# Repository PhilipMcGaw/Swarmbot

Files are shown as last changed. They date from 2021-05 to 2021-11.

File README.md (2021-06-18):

# SwarmBot

## Physical design constraints

* Smallest 3D Printer maximum dimensions 100 x 100 x 100
* Largest Cheap PCB from China 100 x 100 FR4 (50¢ each)

## People who have contributed

 * Philip 'Skippy' McGaw - philip@mcgaw.eu - [philipmcgaw.com](https://philipmcgaw.com)
 * Tamarisk 'NotQuiteHere' McGaw - tamarisk@mcgaw.eu - [tamarisk.it](https://tamarisk.it)
 * Bob 'thinkl33t' Clough - bob@clough.me - [thinkl33t.co.uk](https://thinkl33t.co.uk)

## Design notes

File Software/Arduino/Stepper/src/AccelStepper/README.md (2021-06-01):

This fork follows the [upstream version](http://www.airspayce.com/mikem/arduino/AccelStepper/). Files are slightly reorganised to follow Arduino library conventions to allow for inclusion into the Arduino IDE library manager.

Please direct questions and discussion to [the Google group](http://groups.google.com/group/accelstepper)

---

This is the Arduino AccelStepper library. It provides an object-oriented interface for 2, 3 or 4 pin stepper motors and motor drivers.

The standard Arduino IDE includes the [Stepper library](http://arduino.cc/en/Reference/Stepper) for stepper motors. It is perfectly adequate for simple, single motor applications.

AccelStepper significantly improves on the standard Arduino Stepper library in several ways:

  - Supports acceleration and deceleration
  - Supports multiple simultaneous steppers, with independent concurrent stepping on each stepper
  - API functions never delay() or block
  - Supports 2, 3 and 4 wire steppers, plus 3 and 4 wire half steppers.
  - Supports alternate stepping functions to enable support of [AFMotor](https://github.com/adafruit/Adafruit-Motor-Shield-library)
  - Supports stepper drivers such as the Sparkfun EasyDriver (based on 3967 driver chip)
  - Very slow speeds are supported
  - Extensive API
  - Subclass support

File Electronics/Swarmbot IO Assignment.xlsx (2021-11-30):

Pin # | Function | GPIO Number | ADC Number | PWM | KiCad
1 | GND |  |  |  | GND
2 | 3V3 |  |  |  | 3V3
3 | Enable |  |  |  | enable
4 | Sensor_VP | 36 | 0 | yes | IR 1 | Analouge in
5 | Sensor_VN | 39 | 3 | yes | IR 2 | Analouge in
6 | IO34 | 34 | 6 | yes | IR 3 | Analouge in
7 | IO35 | 35 | 7 | yes | IR 4 | Analouge in
8 | IO32 | 32 | 4 | yes | IR 5 | Analouge in
9 | IO33 | 33 | 5 | yes | Bat V | Analouge in
10 | IO25 | 25 | 18 | yes | Bat I | Analouge in
11 | IO26 | 26 | 19 | yes | Top PCB Version | Analouge in
12 | IO27 | 27 | 17 | yes | Bottom PCB Version | Analouge in
13 | IO14 | 14 | 16 | yes | Line Sensor 5 | Analouge in
14 | IO12 | 12 | 15 | yes | Line Sensor 3 | Analouge in
15 | GND |  |  |  | GND
16 | IO13 | 13 | 14 | yes | Line Sensor 1 | Analouge in
17 | SD2 | 9 |  | yes | Motor PWM 1 | Digital out (PWM)
18 | SD3 | 10 |  | yes | Motor PWM 2 | Digital out (PWM)
19 | CMD | 11 |  | yes | Motor PWM 3 | Digital out (PWM)
20 | CLK | 6 |  | yes | Motor PWM 4 | Digital out (PWM)
21 | SDO | 7 |  | yes | Left Switch | Digital in
22 | SD1 | 8 |  | yes | Line Sensor LED | Digital out
23 | IO15 | 15 | 13 | yes | Line Sensor 4 | Analouge in
24 | IO2 | 2 | 12 | yes | Line Sensor 2 | Analouge in
25 | IO0 | 0 | 11 | yes | program
26 | IO4 | 4 | 10 | yes | IR LEDS | Digital out
27 | IO16 | 16 |  | yes | Pen Servo | Digital in
28 | IO17 | 17 |  | yes | Right Motor Sensor | Digital in
29 | IO5 | 5 |  | yes | 5V Switch 1 | Digital out
30 | IO18 | 18 |  | yes | Left Motor Sensor | Digital in
31 | IO19 | 19 |  | yes | Sonar Echo | Digital in
32 | n/c |  |  |  | n/c
33 | IO21 | 21 |  | yes | Sonar Trigger | Digital out
34 | RXD0 | 3 |  | yes | RX
35 | TXD0 | 1 |  | yes | TX
36 | IO22 | 22 |  | yes | Right Switch | Digital in
37 | IO23 | 23 |  | yes
38 | GND |  |  |  | GND

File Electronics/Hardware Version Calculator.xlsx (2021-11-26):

Input voltage | 3.3 | Hardware revision ID | R1 Value | R2 Value | Vout | Mapped value
Top Value for map | 100 | 1 | 10 | 0 | 0 | 0
 |  | 2 | 47 | 1 | 0.06875 | 2
 |  | 3 | 10 | 1 | 0.3 | 9
 |  | 4 | 4.7 | 1 | 0.5789473684 | 18
 |  | 5 | 2.2 | 1 | 1.03125 | 31
 |  | 6 | 4.7 | 2.2 | 1.052173913 | 32
 |  | 7 | 10 | 10 | 1.65 | 50
 |  | 8 | 4.7 | 10 | 2.244897959 | 68
 |  | 9 | 1 | 2.2 | 2.26875 | 69
 |  | 10 | 2.2 | 10 | 2.704918033 | 82
 |  | 11 | 4.7 | 47 | 3 | 91
 |  | 12 | 2.2 | 47 | 3.152439024 | 96
 |  | 13 | 1 | 47 | 3.23125 | 98
 |  | 14 | 0 | 10 | 3.3 | 100

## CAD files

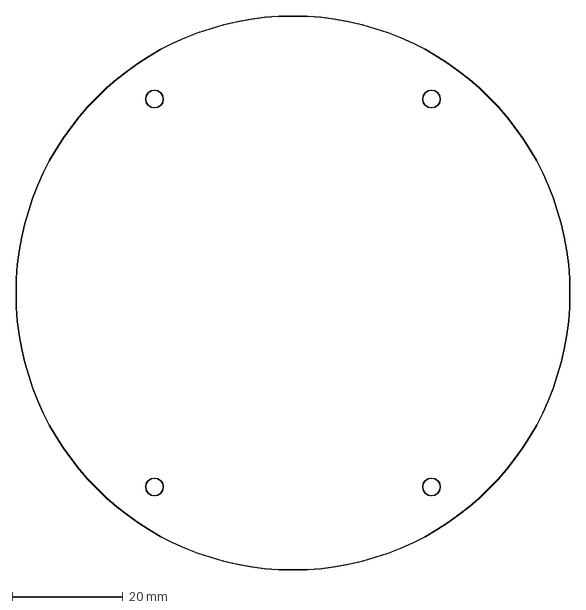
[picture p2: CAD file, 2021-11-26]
Electronics/Swarmbot Top PCB - Edge Cuts.dxf
100.0 x 100.0 mm

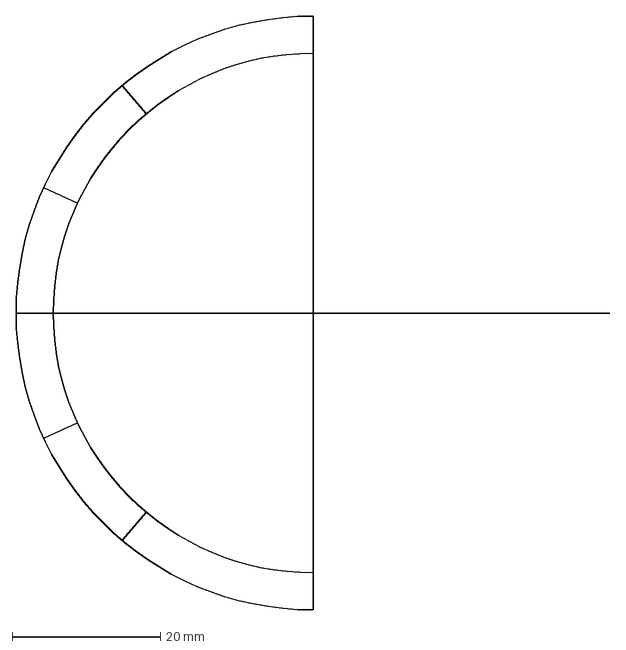
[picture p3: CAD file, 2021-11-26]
Electronics/Swarmbot Top PCB - User.2.dxf
80.0 x 80.0 mm

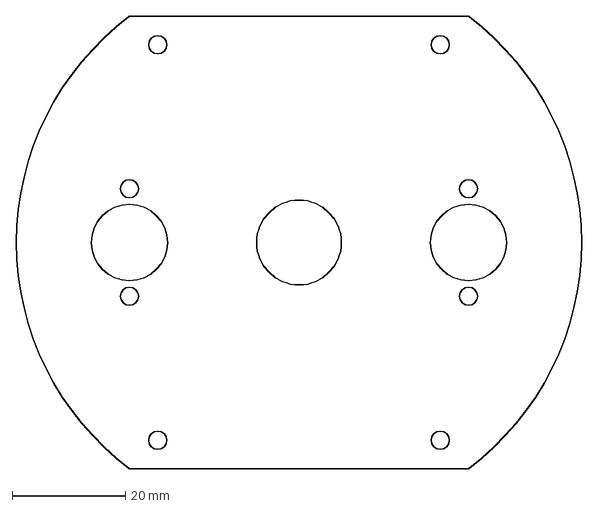
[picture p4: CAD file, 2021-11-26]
Electronics/Swarmbot Bottom PCB - Edge Cuts.dxf
100.0 x 80.0 mm

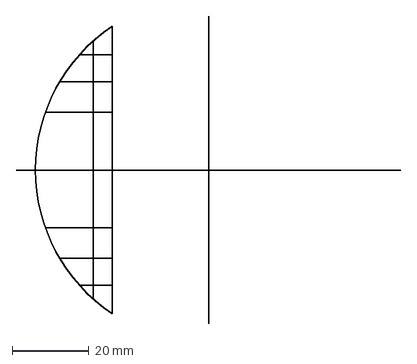
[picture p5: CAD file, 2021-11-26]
Electronics/Swarmbot Bottom PCB - User.2.dxf
100.0 x 80.0 mm

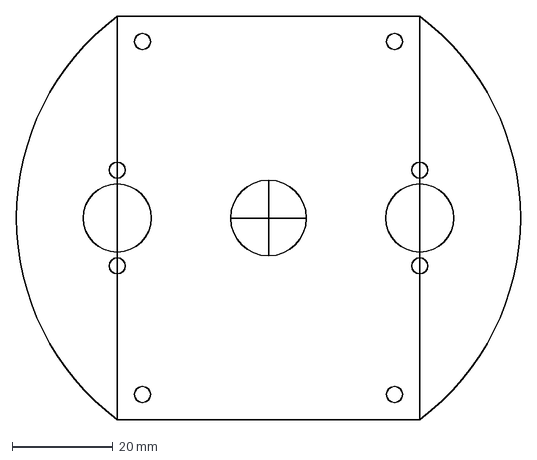
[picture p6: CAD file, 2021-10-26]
Electronics/Swarmbot v2.dxf
100.0 x 80.0 mm

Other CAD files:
Mechanical/Swarmbot Assembly.f3d

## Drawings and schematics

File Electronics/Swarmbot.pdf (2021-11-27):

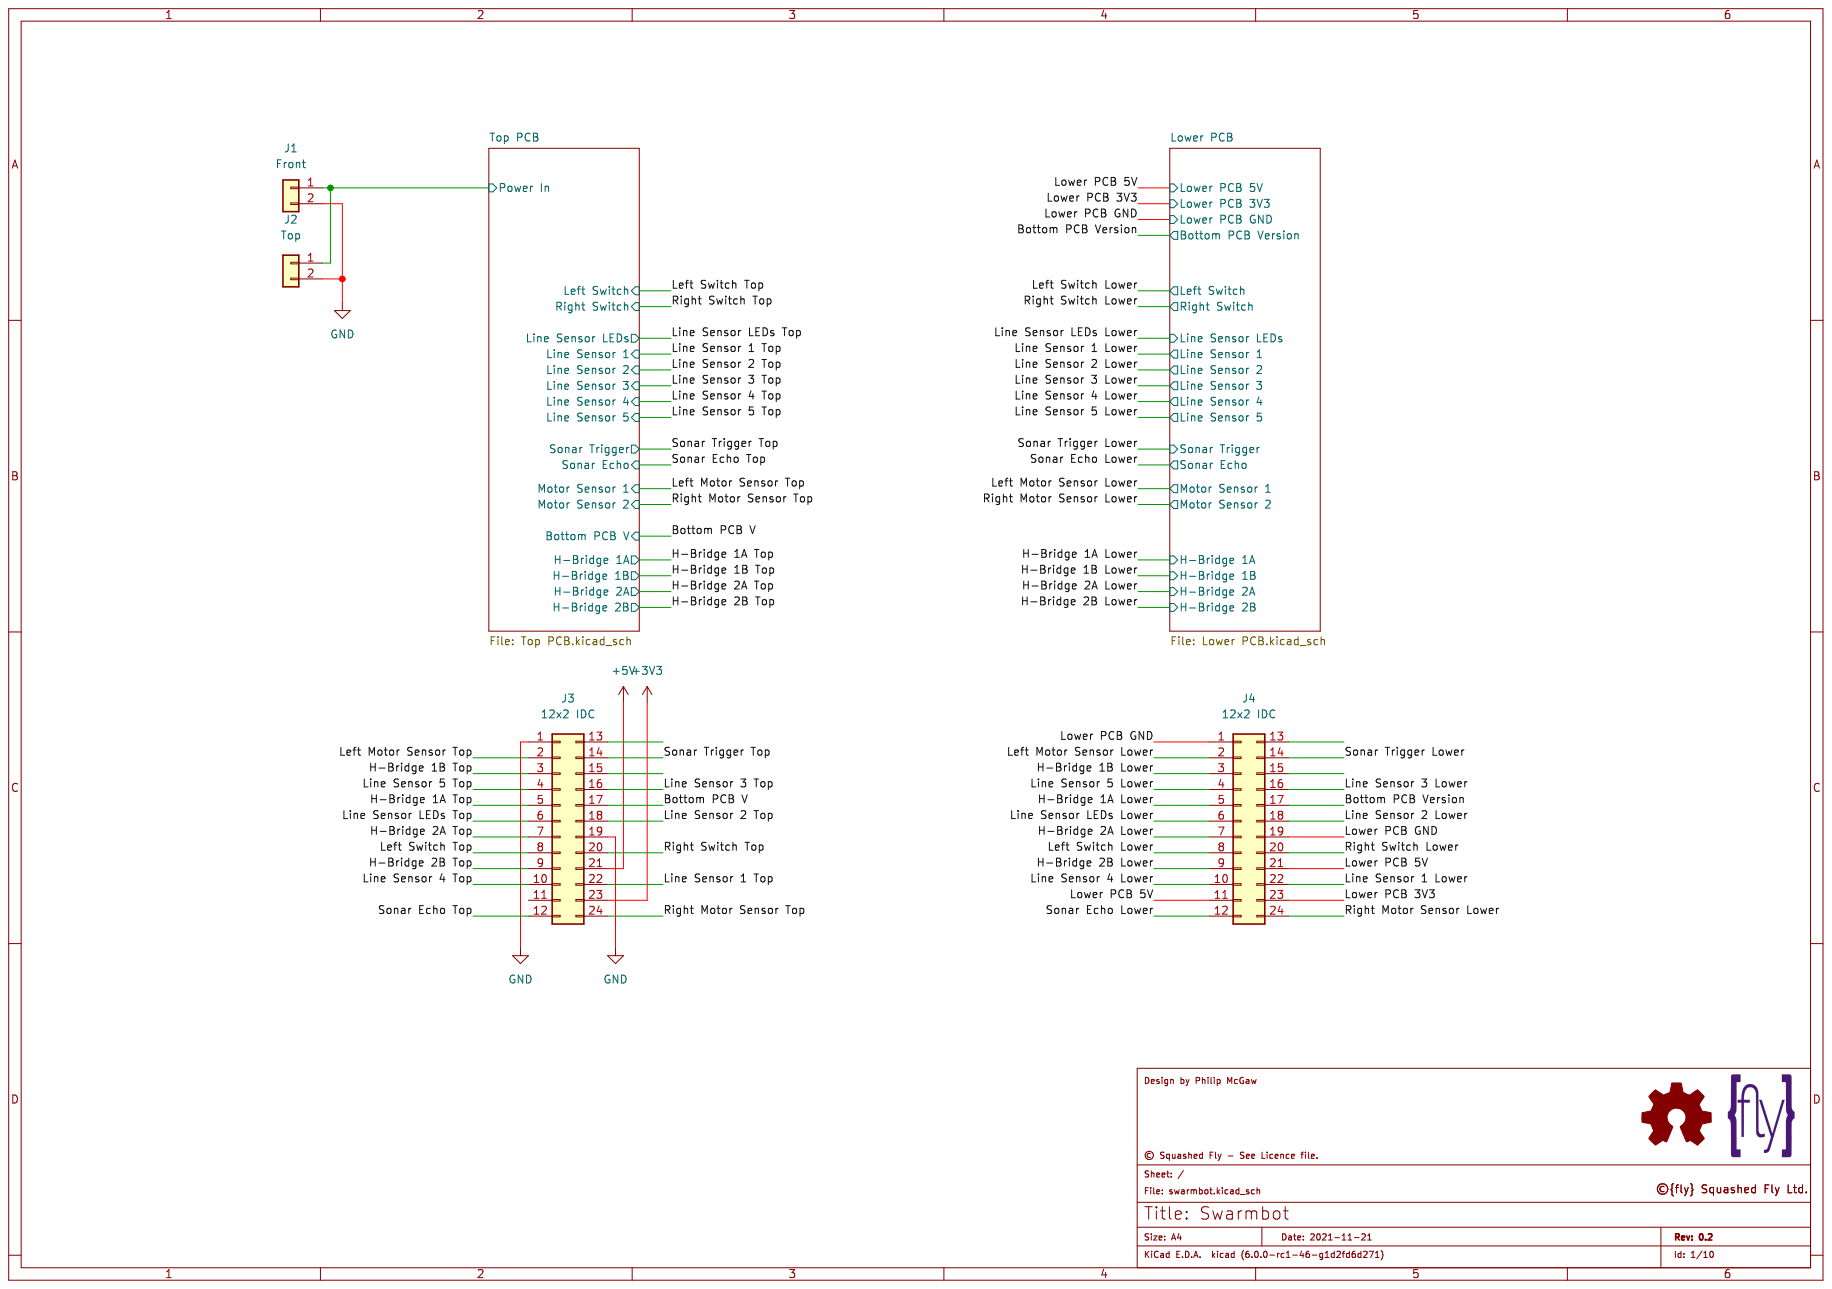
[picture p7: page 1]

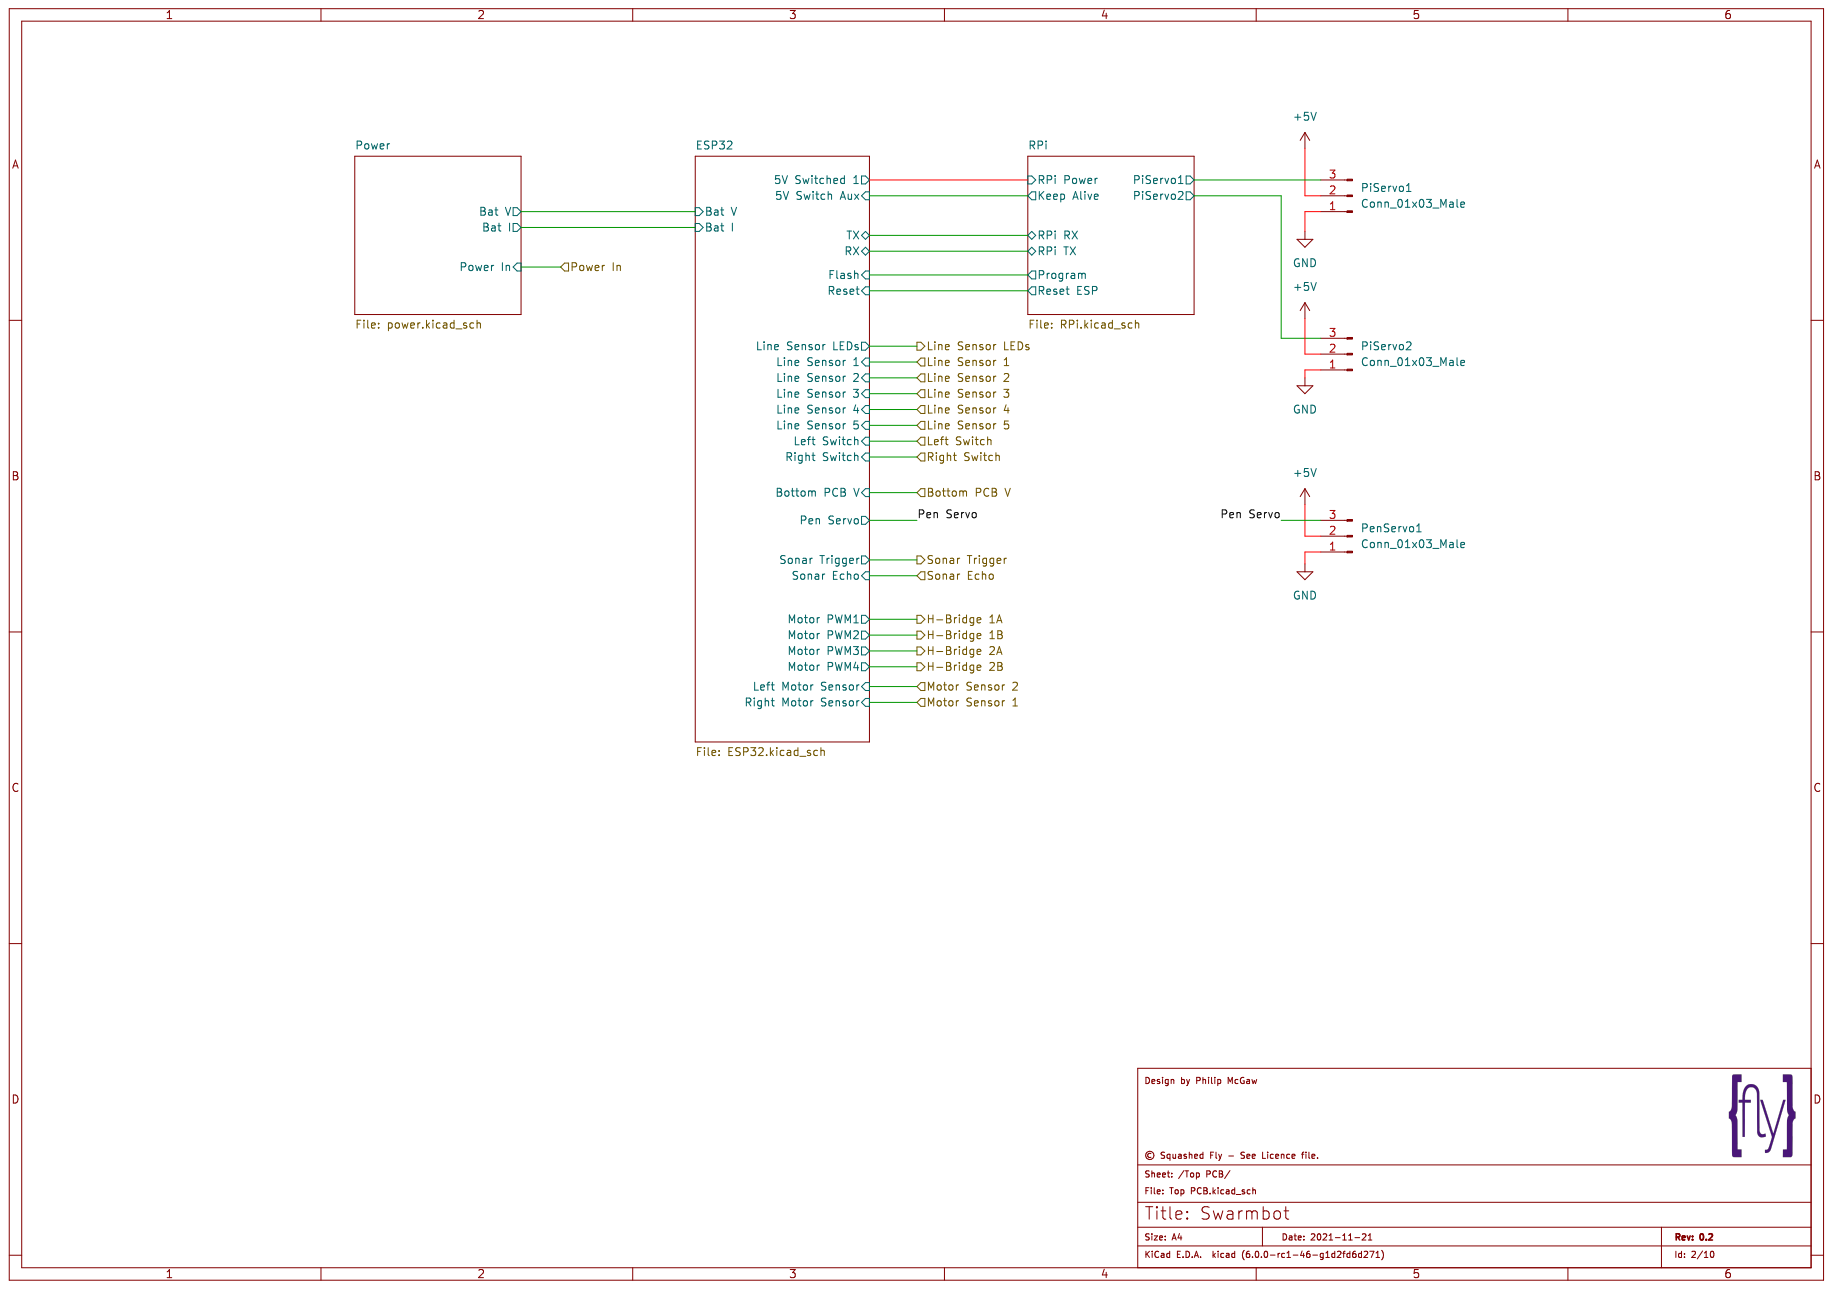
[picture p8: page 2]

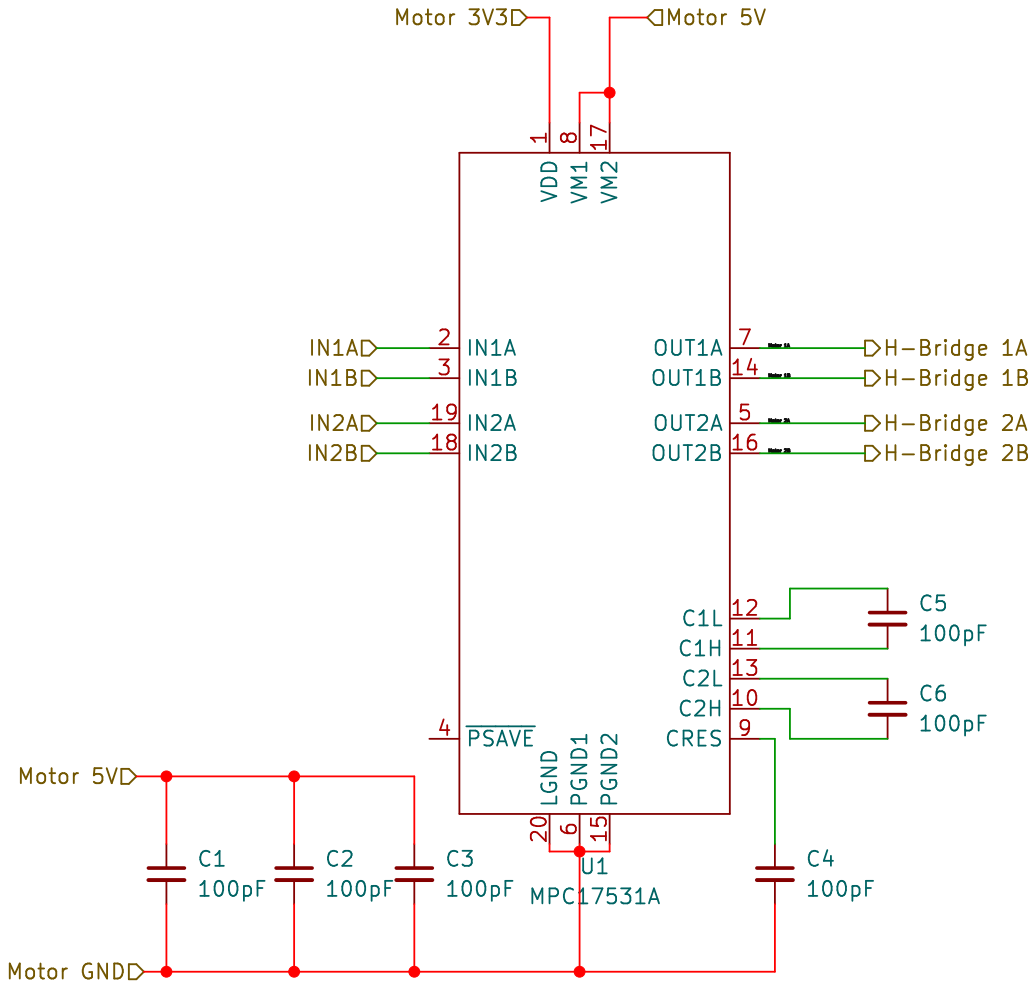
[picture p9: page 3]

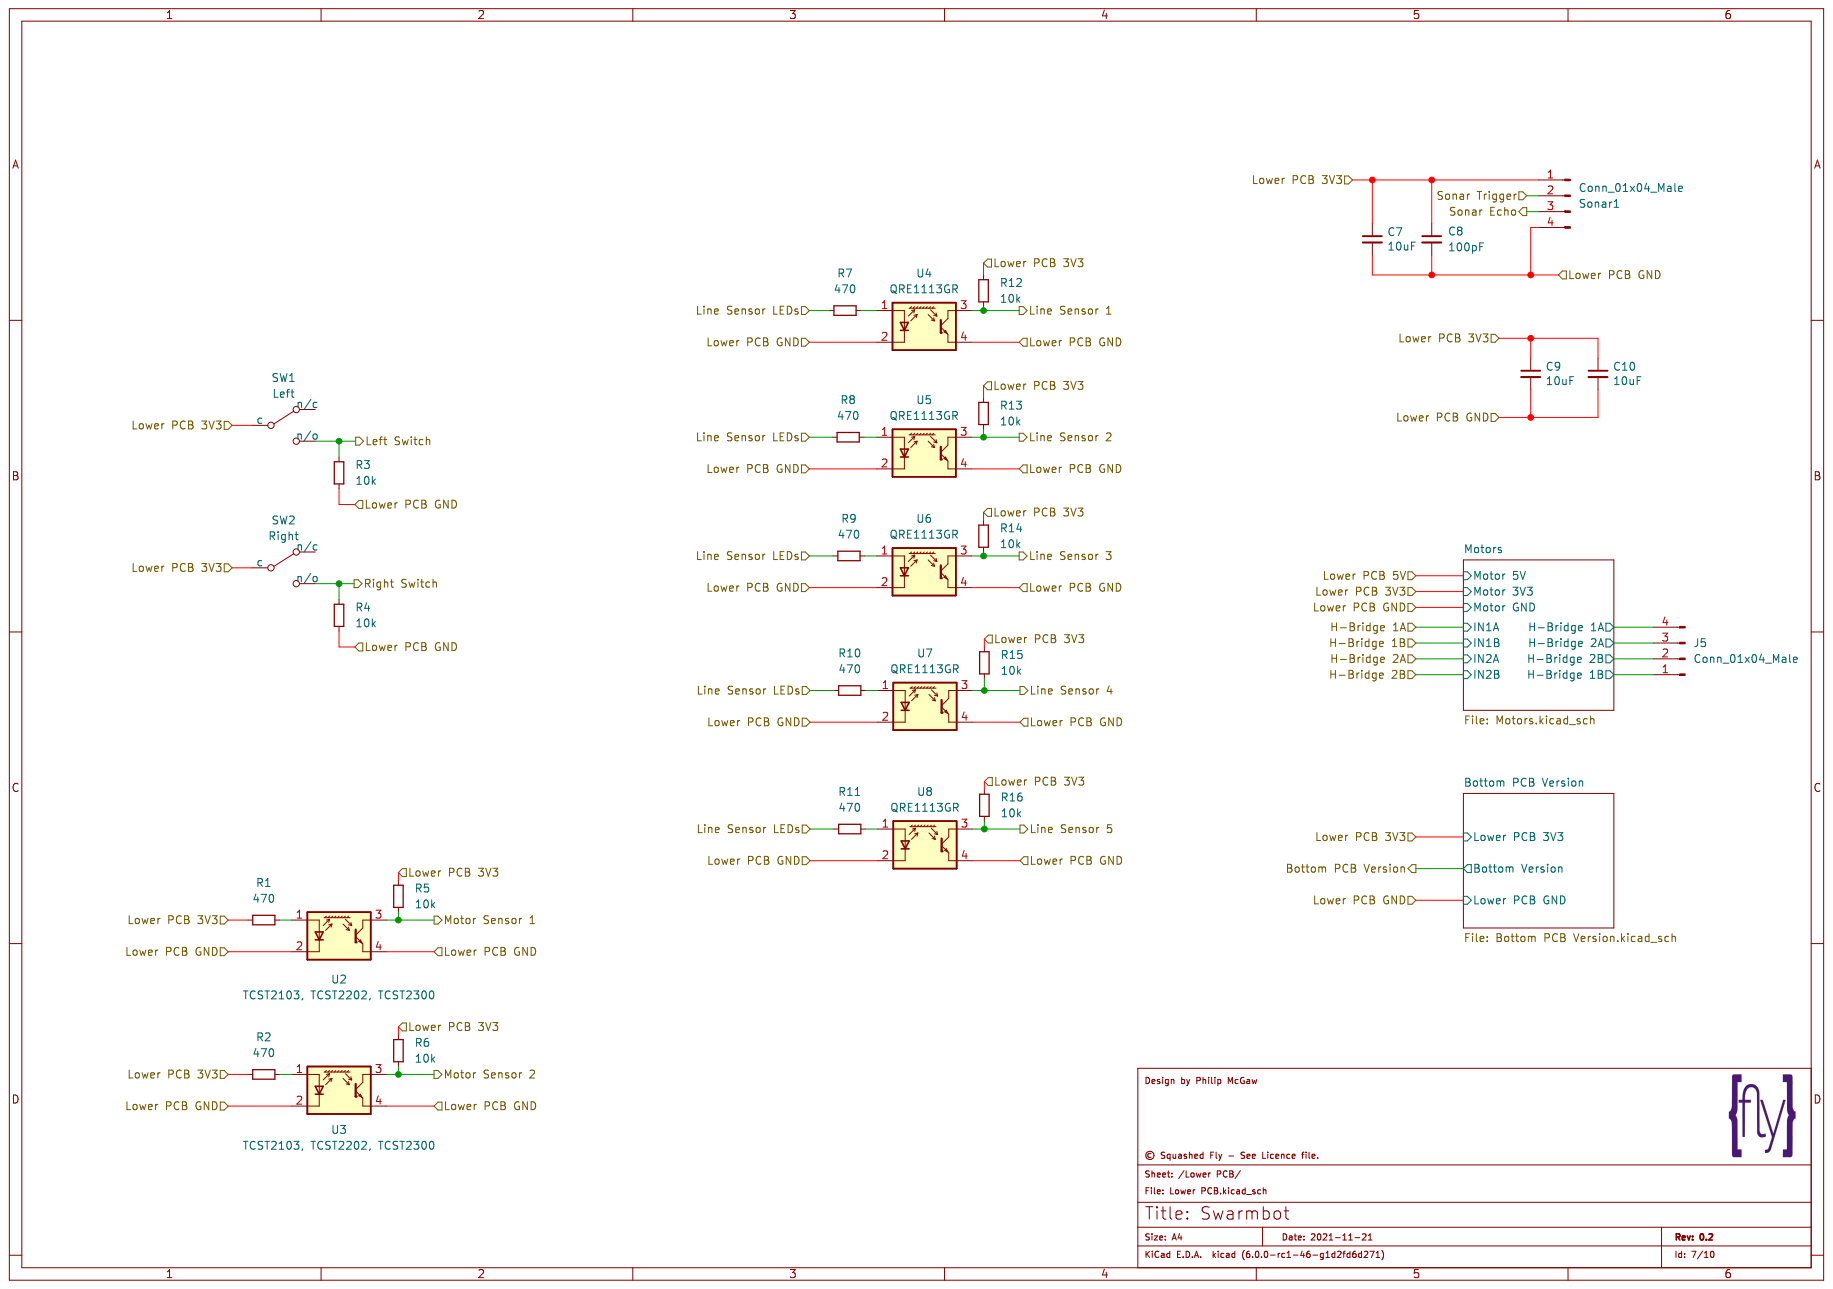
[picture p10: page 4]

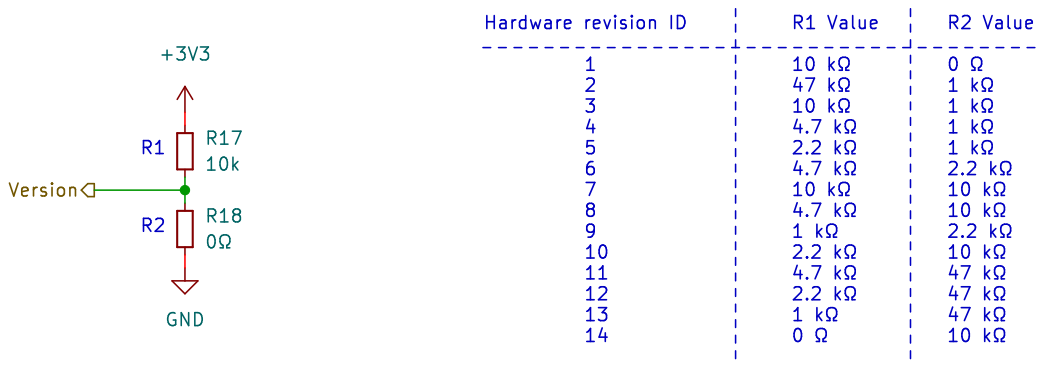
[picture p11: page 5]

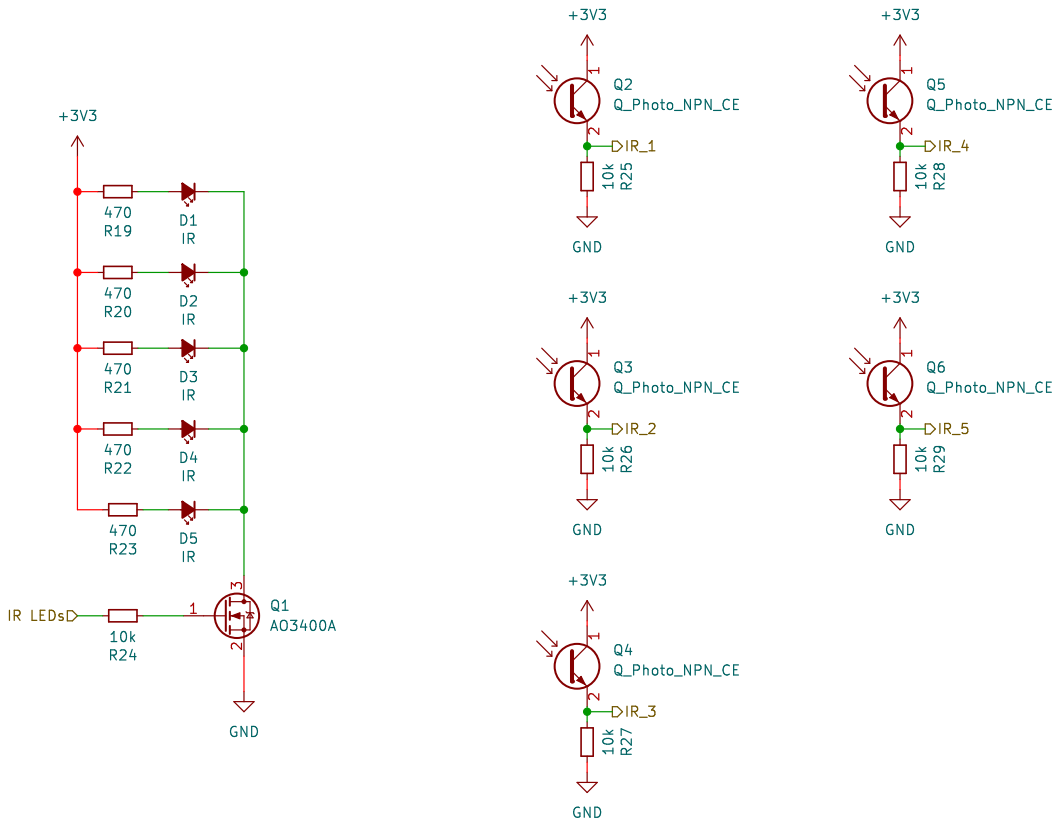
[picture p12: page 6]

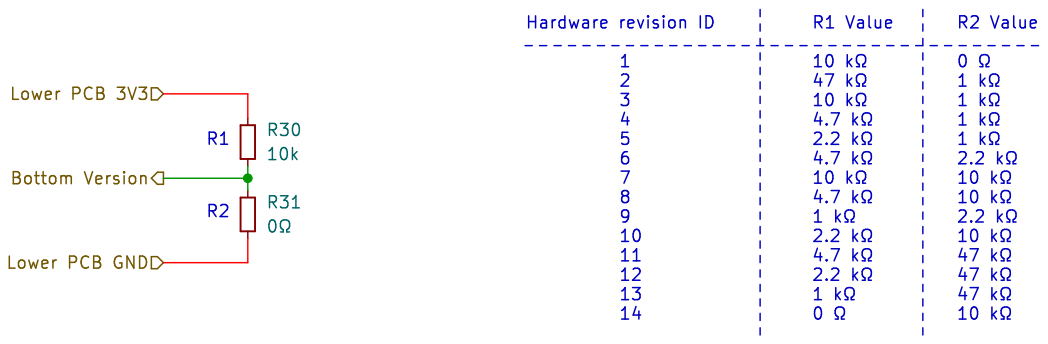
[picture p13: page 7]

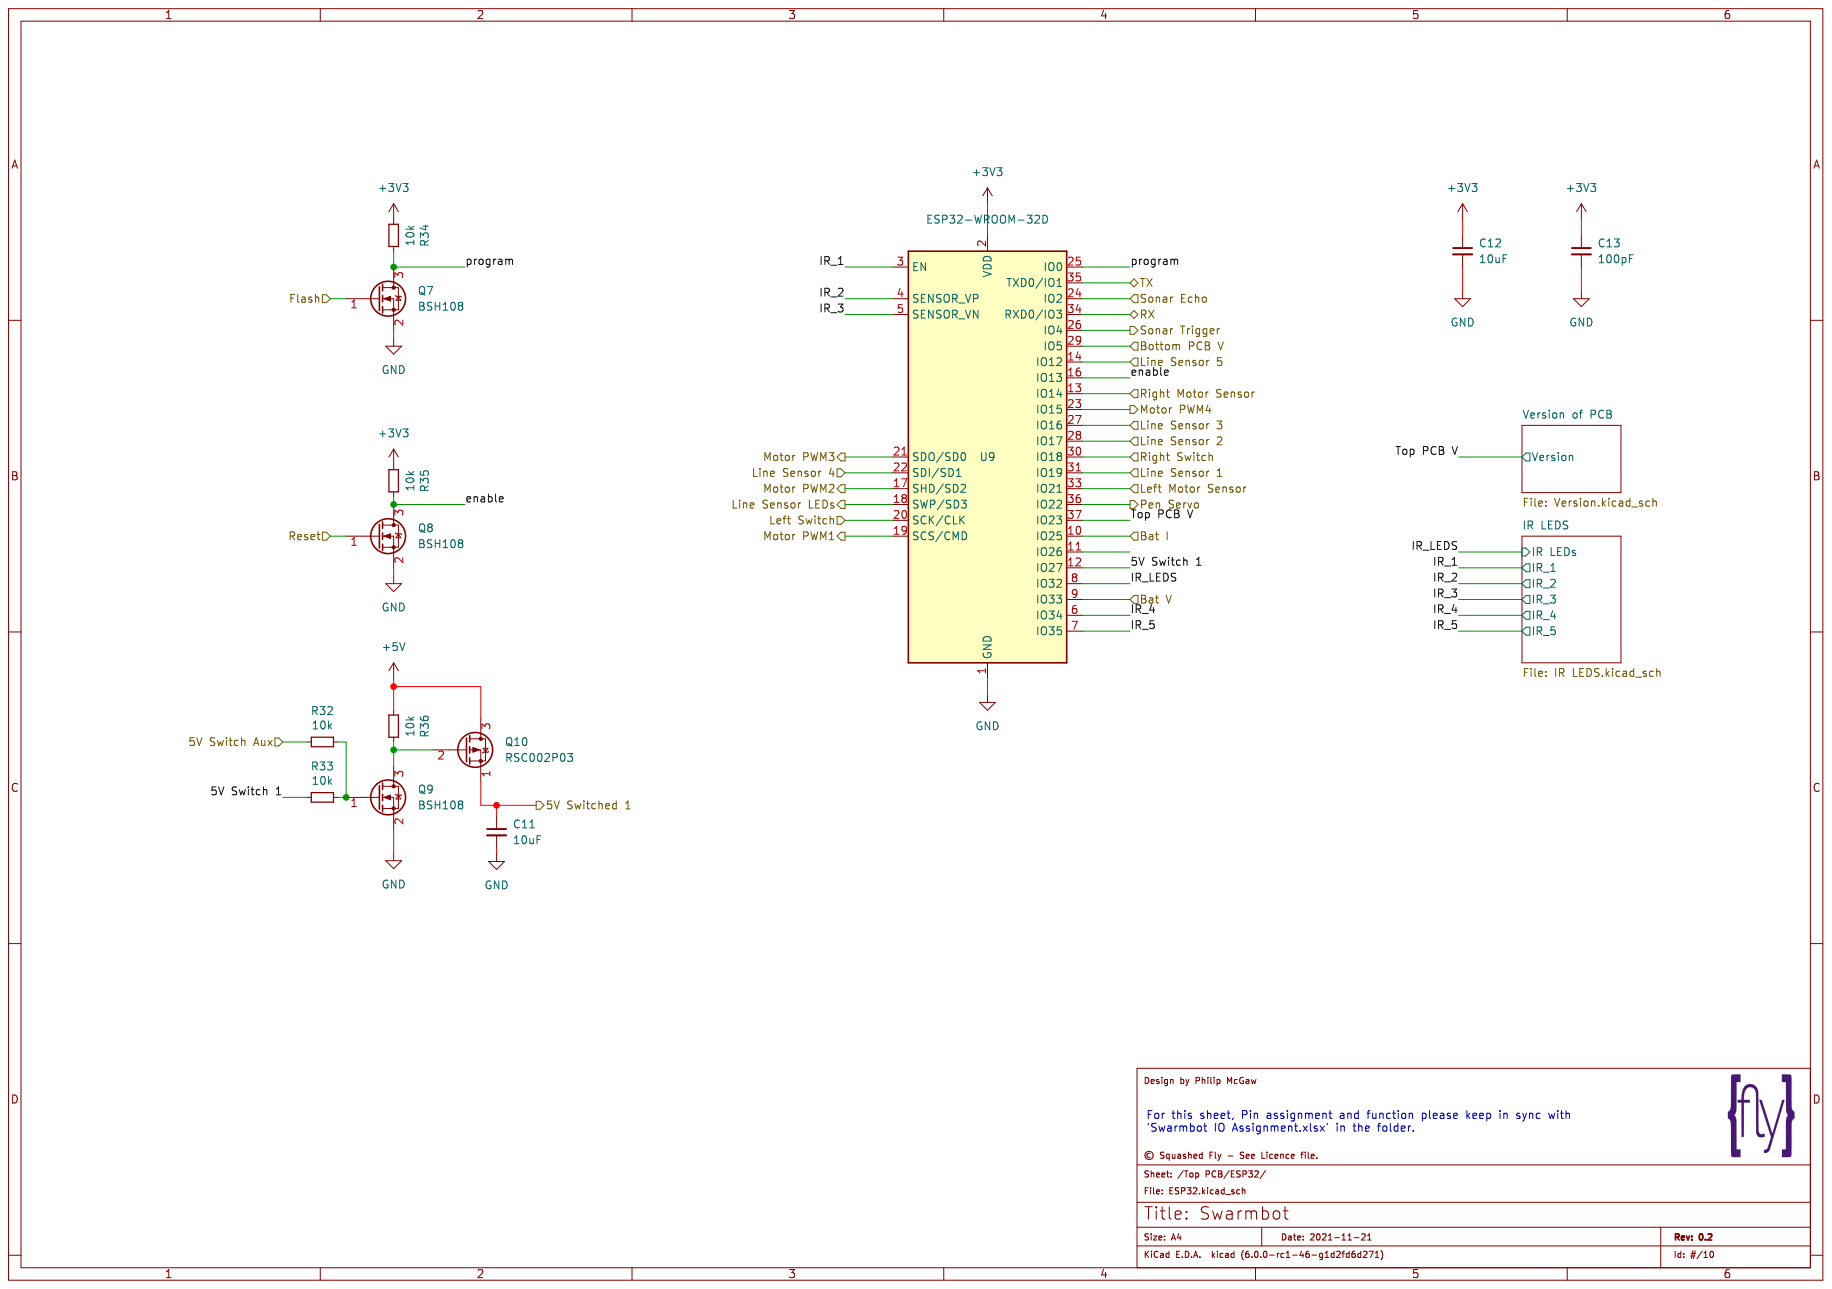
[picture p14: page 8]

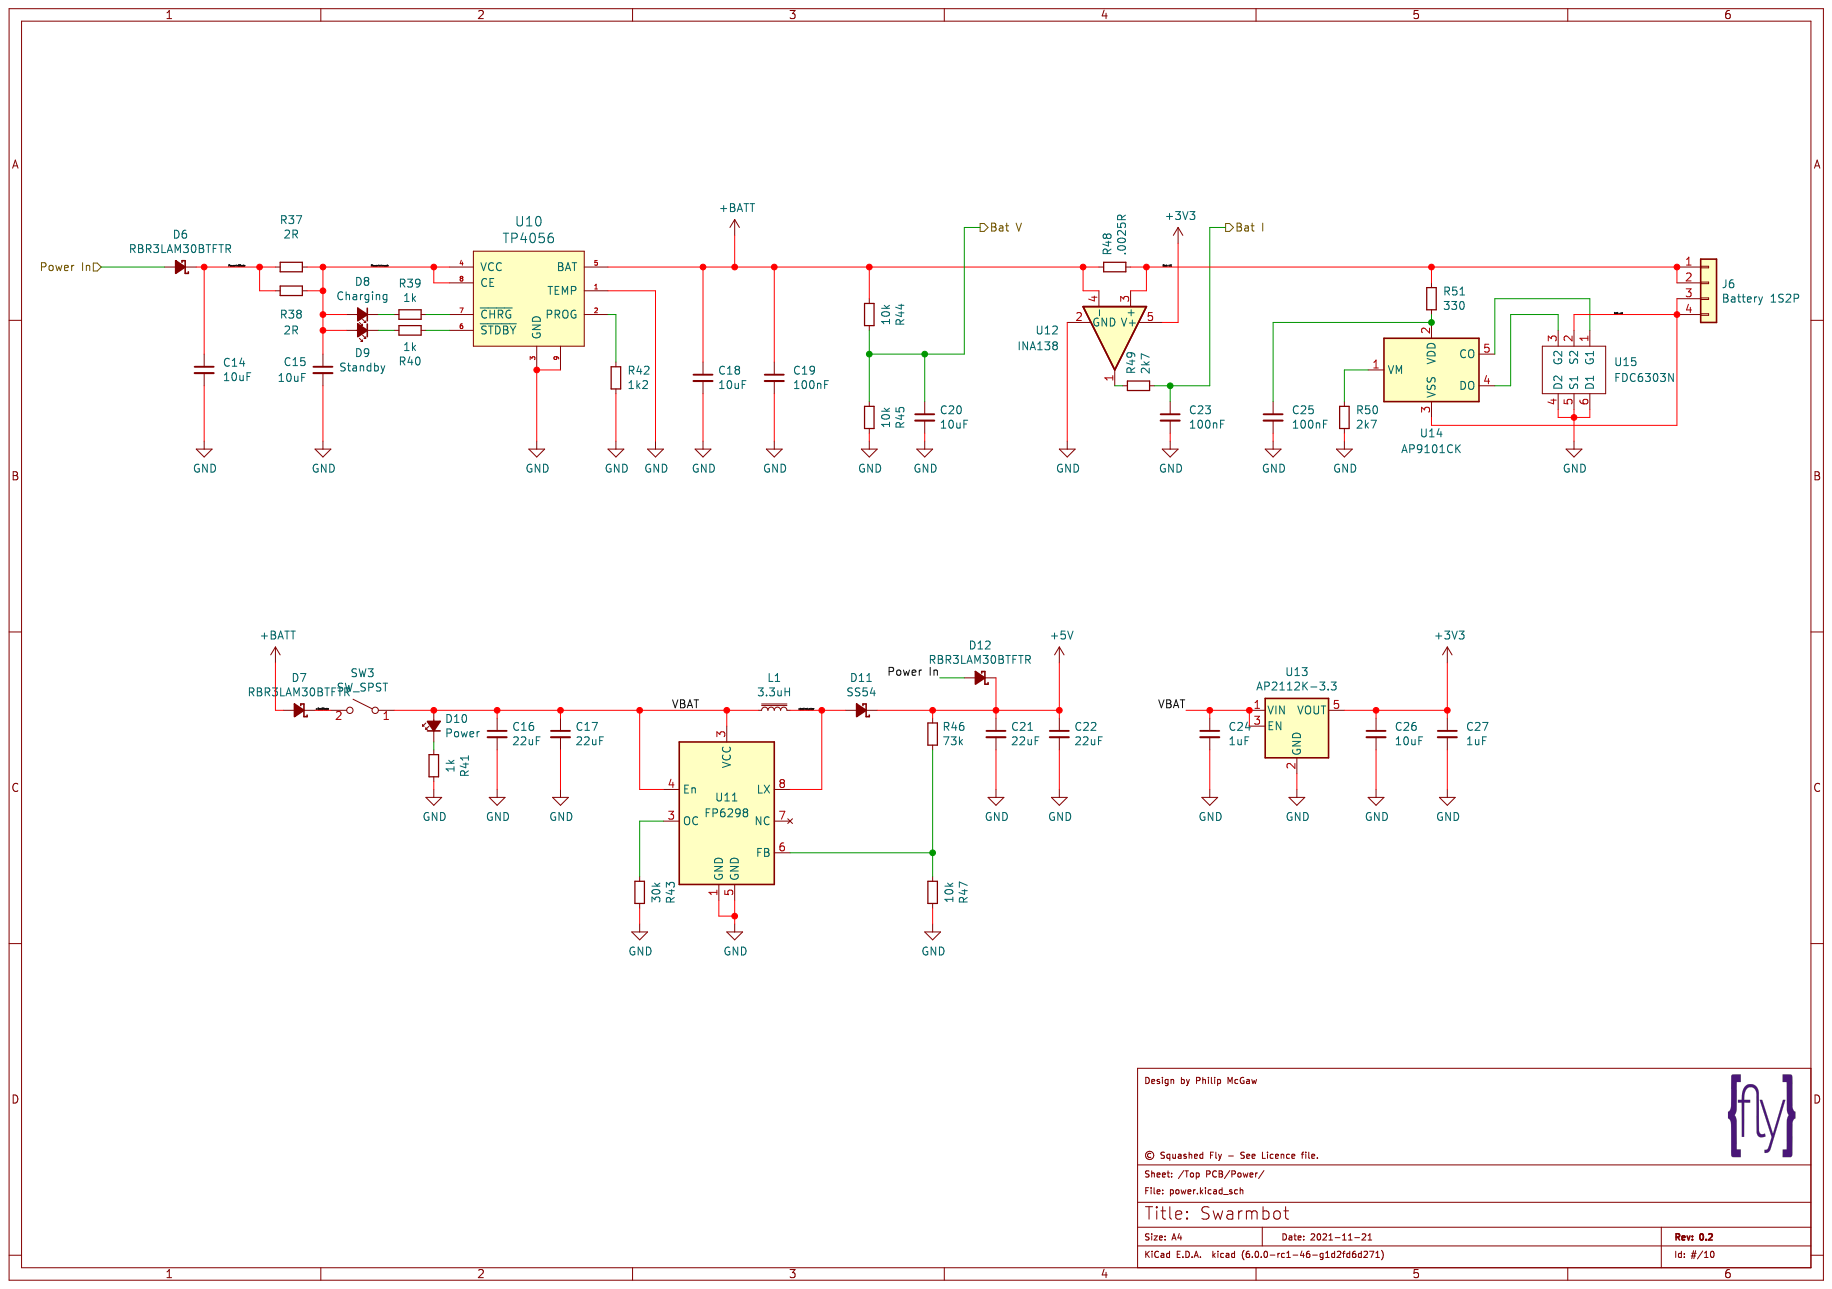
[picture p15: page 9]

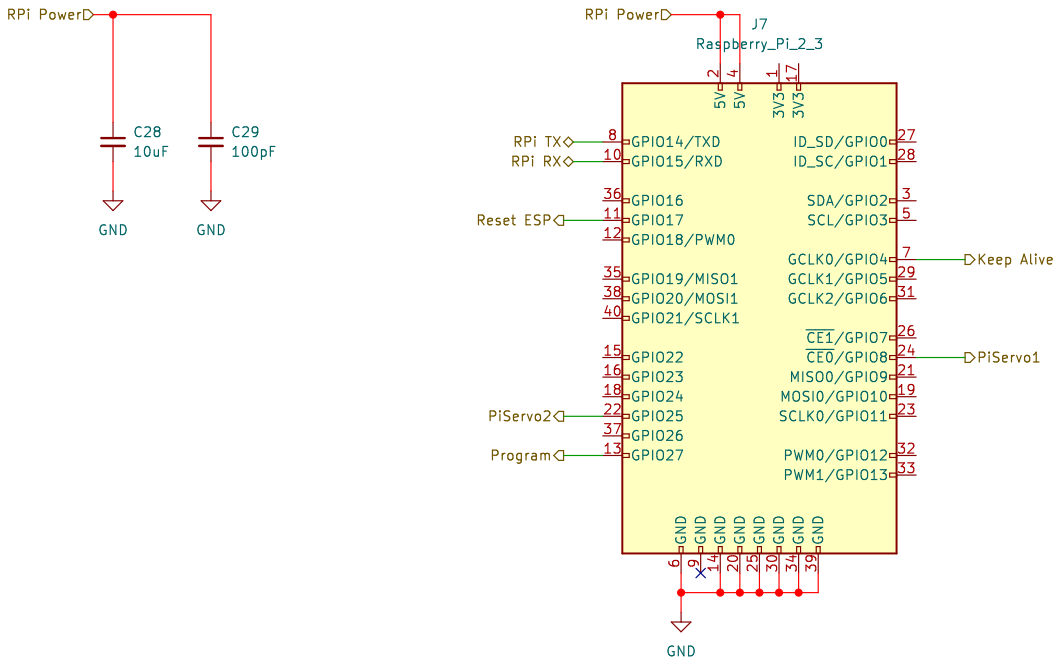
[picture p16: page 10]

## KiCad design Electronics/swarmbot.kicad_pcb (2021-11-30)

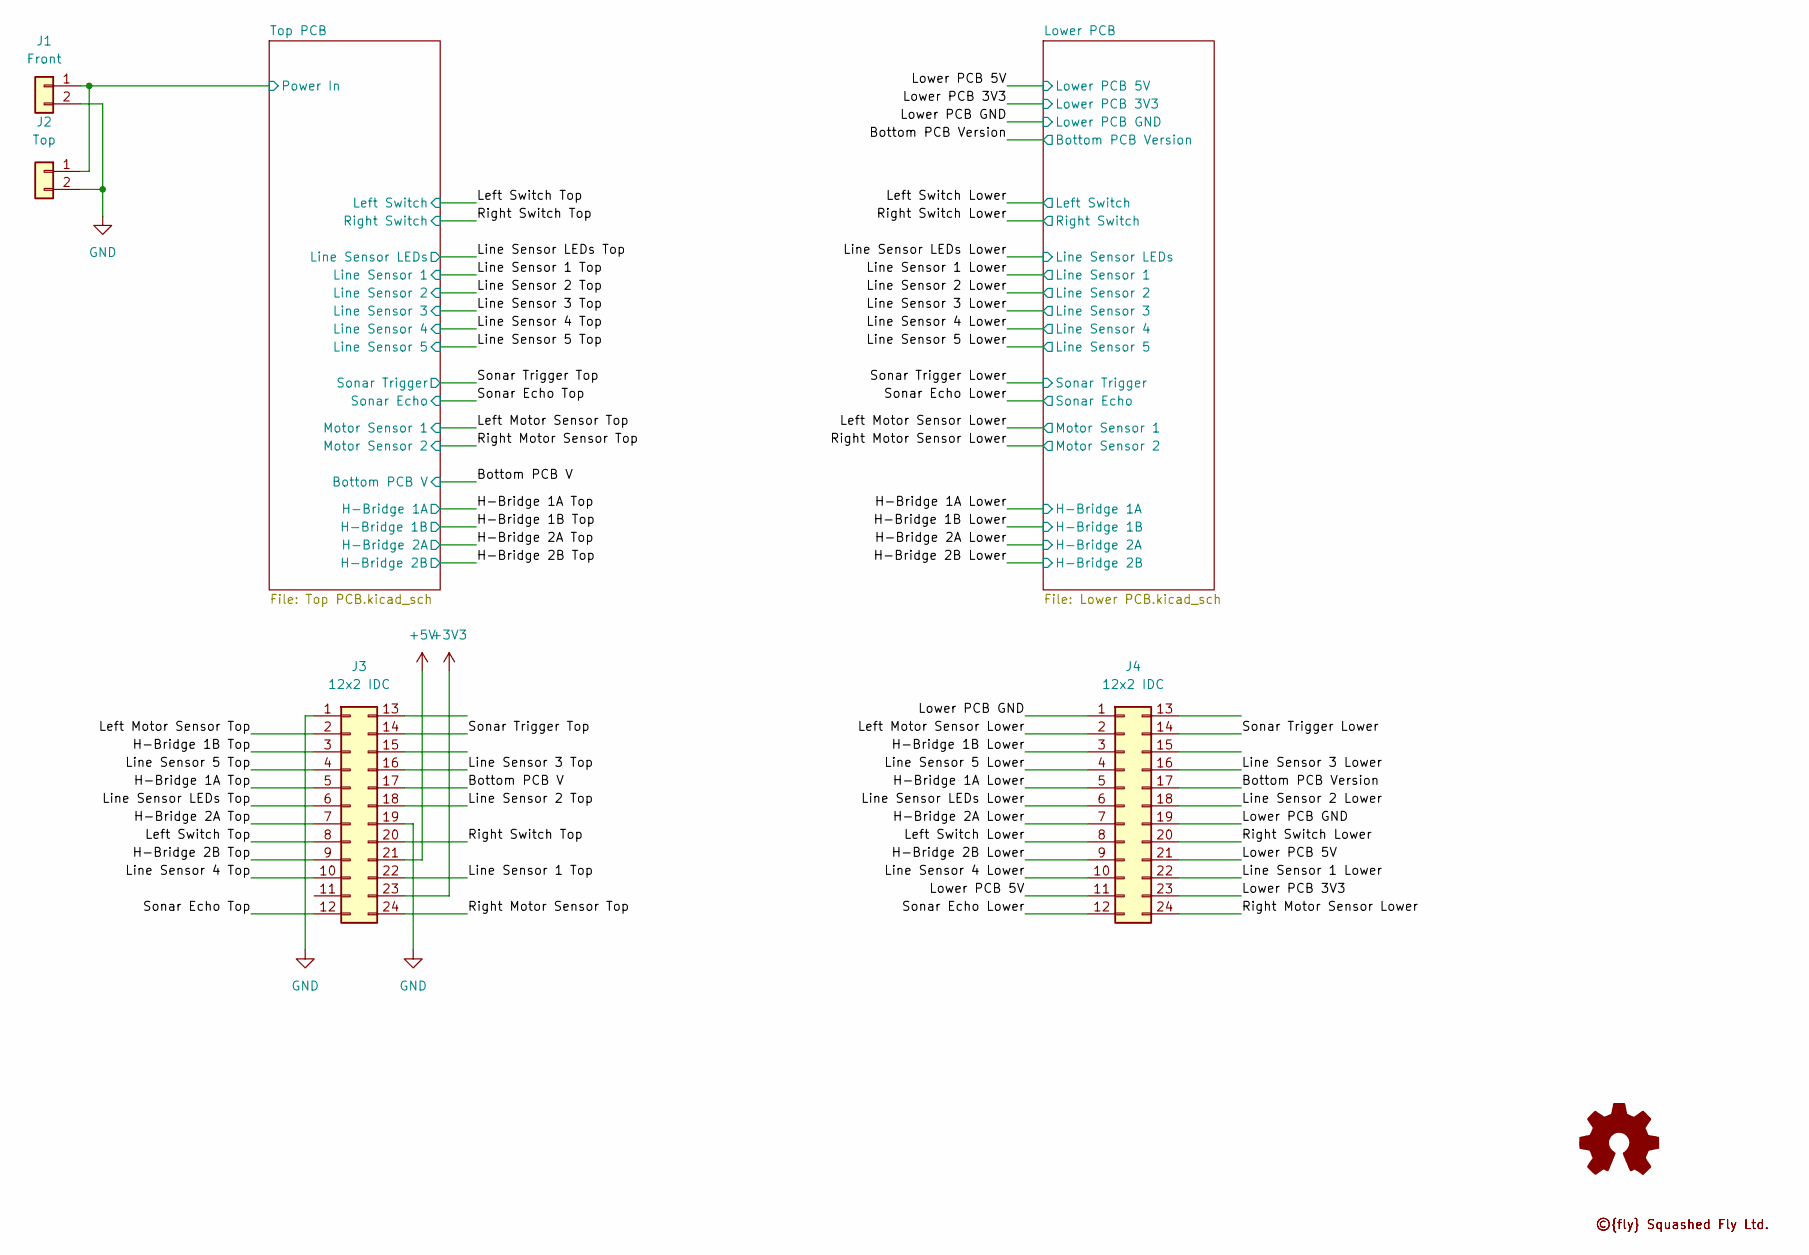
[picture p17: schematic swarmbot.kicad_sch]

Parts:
J1: Front; JST_XH_B2B-XH-A_1x02_P2.50mm_Vertical
J2: Top; JST_XH_B2B-XH-A_1x02_P2.50mm_Vertical
J3, J4: 12x2 IDC; IDC-Header_2x12_P2.54mm_Vertical
LOGO1: Logo_Open_Hardware_Small; OSHW-Logo2_7.3x6mm_SilkScreen
Logo1, Logo2: SquashedFlyLogo; SquashedFlySilk

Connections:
+3V3: J3.23; also elsewhere on the board
+5V: J3.21; also elsewhere on the board
/Bottom PCB V: J3.17; also elsewhere on the board
/Bottom PCB Version: J4.17; also elsewhere on the board
/H-Bridge 1A Lower: J4.5; also elsewhere on the board
/H-Bridge 1A Top: J3.5; also elsewhere on the board
/H-Bridge 1B Lower: J4.3; also elsewhere on the board
/H-Bridge 1B Top: J3.3; also elsewhere on the board
/H-Bridge 2A Lower: J4.7; also elsewhere on the board
/H-Bridge 2A Top: J3.7; also elsewhere on the board
/H-Bridge 2B Lower: J4.9; also elsewhere on the board
/H-Bridge 2B Top: J3.9; also elsewhere on the board
/Left Motor Sensor Lower: J4.2; also elsewhere on the board
/Left Motor Sensor Top: J3.2; also elsewhere on the board
/Left Switch Lower: J4.8; also elsewhere on the board
/Left Switch Top: J3.8; also elsewhere on the board
/Line Sensor 1 Lower: J4.22; also elsewhere on the board
/Line Sensor 1 Top: J3.22; also elsewhere on the board
/Line Sensor 2 Lower: J4.18; also elsewhere on the board
/Line Sensor 2 Top: J3.18; also elsewhere on the board
/Line Sensor 3 Lower: J4.16; also elsewhere on the board
/Line Sensor 3 Top: J3.16; also elsewhere on the board
/Line Sensor 4 Lower: J4.10; also elsewhere on the board
/Line Sensor 4 Top: J3.10; also elsewhere on the board
/Line Sensor 5 Lower: J4.4; also elsewhere on the board
/Line Sensor 5 Top: J3.4; also elsewhere on the board
/Line Sensor LEDs Lower: J4.6; also elsewhere on the board
/Line Sensor LEDs Top: J3.6; also elsewhere on the board
/Lower PCB 3V3: J4.23; also elsewhere on the board
/Lower PCB 5V: J4.11, J4.21; also elsewhere on the board
/Lower PCB GND: J4.1, J4.19; also elsewhere on the board
/Right Motor Sensor Lower: J4.24; also elsewhere on the board
/Right Motor Sensor Top: J3.24; also elsewhere on the board
/Right Switch Lower: J4.20; also elsewhere on the board
/Right Switch Top: J3.20; also elsewhere on the board
/Sonar Echo Lower: J4.12; also elsewhere on the board
/Sonar Echo Top: J3.12; also elsewhere on the board
/Sonar Trigger Lower: J4.14; also elsewhere on the board
/Sonar Trigger Top: J3.14; also elsewhere on the board
/Top PCB/Power/Power In: J1.1, J2.1; also elsewhere on the board
GND: J1.2, J2.2, J3.1, J3.19; also elsewhere on the board

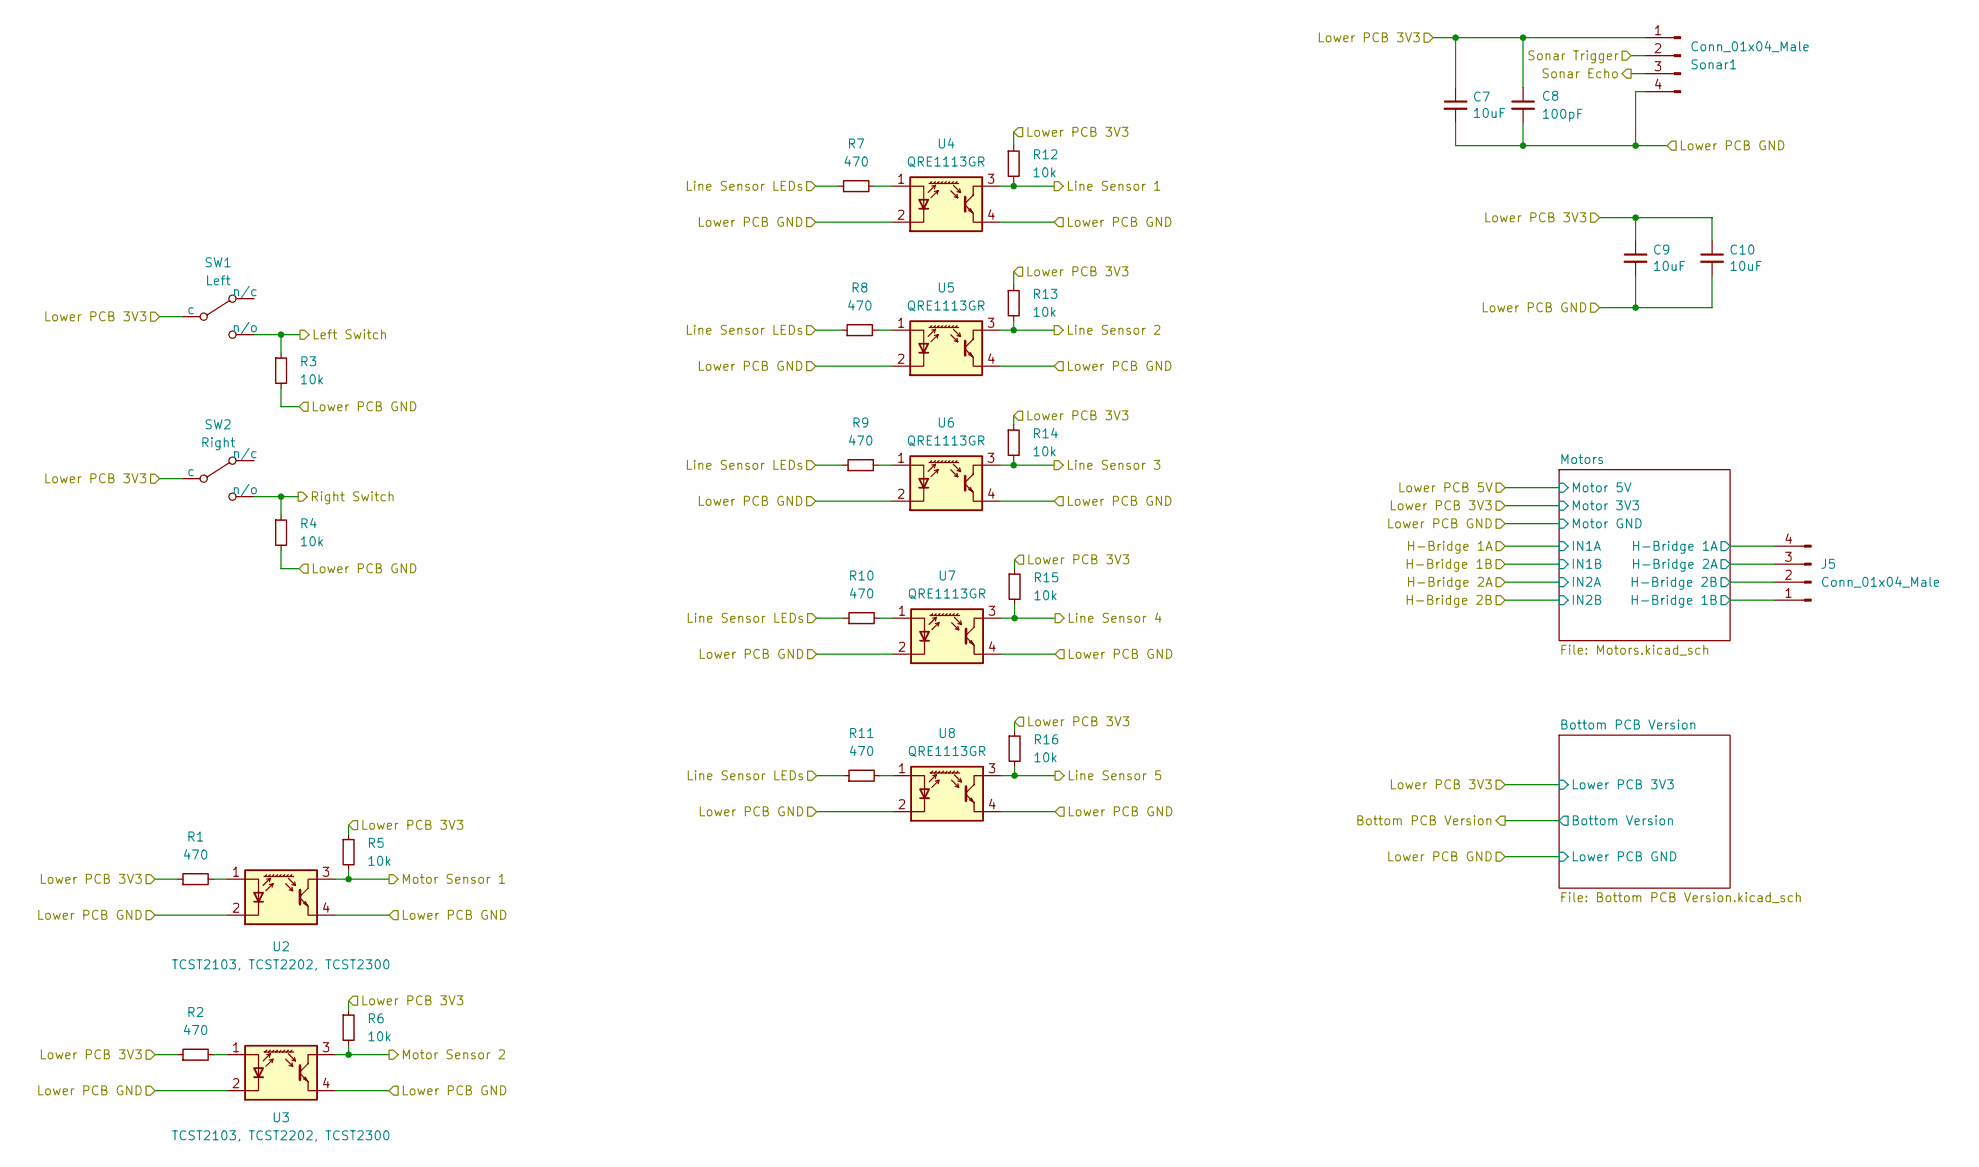
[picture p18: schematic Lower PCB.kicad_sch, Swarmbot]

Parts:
C7, C9, C10: 10uF; C_0805_2012Metric_Pad1.18x1.45mm_HandSolder
C8: 100pF; C_0805_2012Metric_Pad1.18x1.45mm_HandSolder
J5: Conn_01x04_Male; JST_PH_B4B-PH-K_1x04_P2.00mm_Vertical
R1, R2, R7, R8, R9, R10, R11: 470; R_0805_2012Metric_Pad1.20x1.40mm_HandSolder
R3, R4, R5, R6, R12, R13, R14, R15, R16: 10k; R_0805_2012Metric_Pad1.20x1.40mm_HandSolder
SW1: Left; TypeD
SW2: Right; TypeC
Sonar1: Conn_01x04_Male; PinSocket_1x04_P2.54mm_Vertical
U2, U3: TCST2103, TCST2202, TCST2300
U4, U5, U6, U7, U8: QRE1113GR; OnSemi_CASE100CY

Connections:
/Left Motor Sensor Lower: R5.2, U2.3; also elsewhere on the board
/Left Switch Lower: R3.1, SW1.2 (n/o); also elsewhere on the board
/Line Sensor 1 Lower: R12.2, U4.3; also elsewhere on the board
/Line Sensor 2 Lower: R13.2, U5.3; also elsewhere on the board
/Line Sensor 3 Lower: R14.2, U6.3; also elsewhere on the board
/Line Sensor 4 Lower: R15.2, U7.3; also elsewhere on the board
/Line Sensor 5 Lower: R16.2, U8.3; also elsewhere on the board
/Line Sensor LEDs Lower: R7.1, R8.1, R9.1, R10.1, R11.1; also elsewhere on the board
/Lower PCB 3V3: C7.1, C8.1, C9.1, C10.1, R1.1, R2.1, R5.1, R6.1, R12.1, R13.1, R14.1, R15.1, R16.1, SW1.1 (c), SW2.1 (c), Sonar1.1; also elsewhere on the board
/Lower PCB GND: C7.2, C8.2, C9.2, C10.2, R3.2, R4.2, Sonar1.4, U2.2 (K), U2.4, U3.2 (K), U3.4, U4.2 (K), U4.4, U5.2 (K), U5.4, U6.2 (K), U6.4, U7.2 (K), U7.4, U8.2 (K), U8.4; also elsewhere on the board
/Lower PCB/Motors/Motor 1A: J5.4; also elsewhere on the board
/Lower PCB/Motors/Motor 1B: J5.1; also elsewhere on the board
/Lower PCB/Motors/Motor 2A: J5.3; also elsewhere on the board
/Lower PCB/Motors/Motor 2B: J5.2; also elsewhere on the board
/Right Motor Sensor Lower: R6.2, U3.3; also elsewhere on the board
/Right Switch Lower: R4.1, SW2.2 (n/o); also elsewhere on the board
/Sonar Echo Lower: Sonar1.3; also elsewhere on the board
/Sonar Trigger Lower: Sonar1.2; also elsewhere on the board
unnamed: R1.2, U2.1 (A)
unnamed: R2.2, U3.1 (A)
unnamed: R7.2, U4.1 (A)
unnamed: R8.2, U5.1 (A)
unnamed: R9.2, U6.1 (A)
unnamed: R10.2, U7.1 (A)
unnamed: R11.2, U8.1 (A)

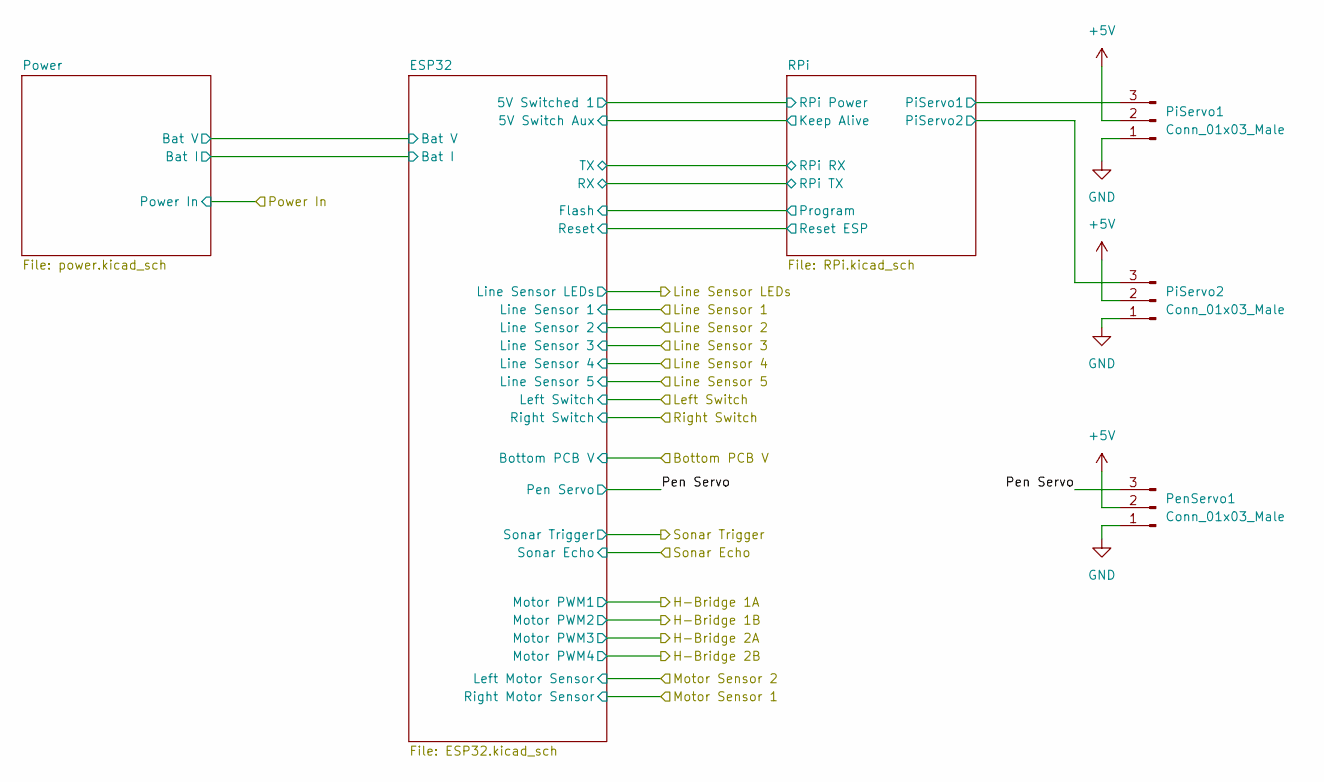
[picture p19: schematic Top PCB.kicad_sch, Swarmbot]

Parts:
PenServo1: Conn_01x03_Male; PinHeader_1x03_P2.54mm_Vertical
PiServo1, PiServo2: Conn_01x03_Male; PinHeader_1x03_P2.54mm_Vertical

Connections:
+5V: PenServo1.2, PiServo1.2, PiServo2.2; also elsewhere on the board
/Top PCB/Pen Servo: PenServo1.3; also elsewhere on the board
/Top PCB/RPi/PiServo1: PiServo1.3; also elsewhere on the board
/Top PCB/RPi/PiServo2: PiServo2.3; also elsewhere on the board
GND: PenServo1.1, PiServo1.1, PiServo2.1; also elsewhere on the board

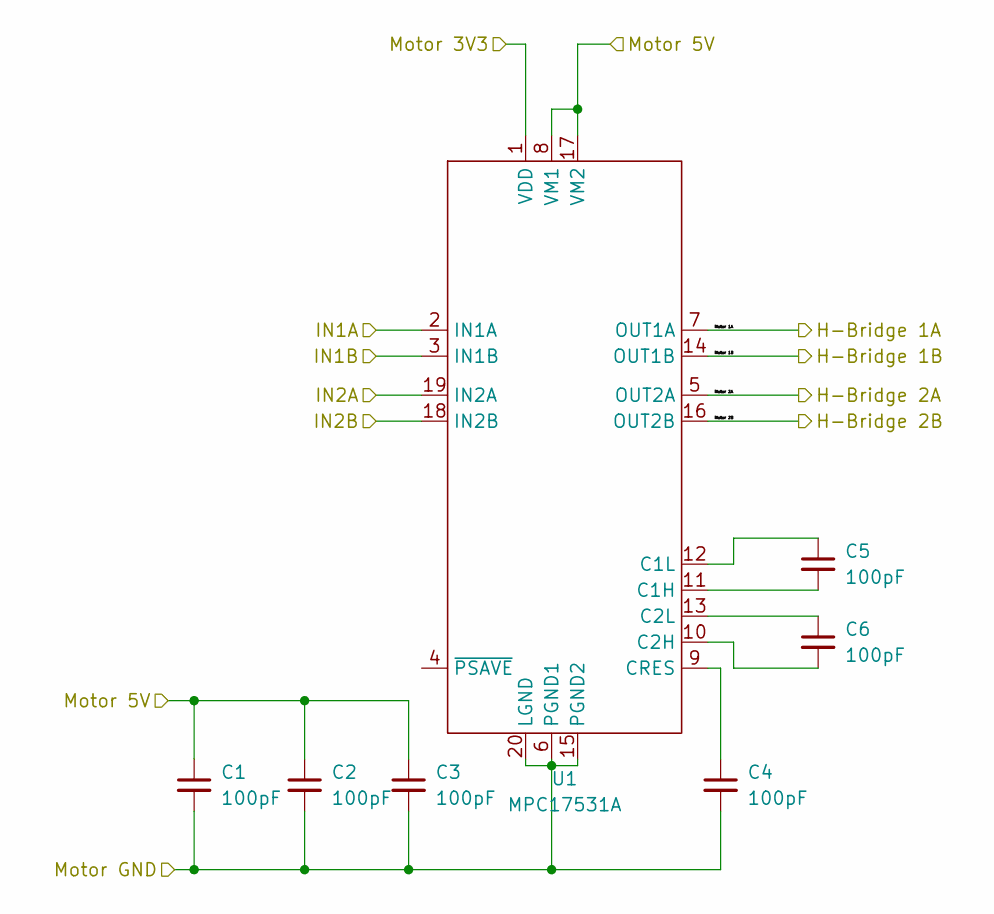
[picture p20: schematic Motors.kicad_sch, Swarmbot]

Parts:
C1, C2, C3, C4, C5, C6: 100pF; C_0805_2012Metric_Pad1.18x1.45mm_HandSolder
U1: MPC17531A; HTSSOP-20-1EP_4.4x6.5mm_P0.65mm_EP3.4x6.5mm_Mask2.75x3.43mm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; Farnell 2890075

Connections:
/H-Bridge 1A Lower: U1.2 (IN1A); also elsewhere on the board
/H-Bridge 1B Lower: U1.3 (IN1B); also elsewhere on the board
/H-Bridge 2A Lower: U1.19 (IN2A); also elsewhere on the board
/H-Bridge 2B Lower: U1.18 (IN2B); also elsewhere on the board
/Lower PCB 3V3: U1.1 (VDD); also elsewhere on the board
/Lower PCB 5V: C1.1, C2.1, C3.1, U1.8 (VM1), U1.17 (VM2); also elsewhere on the board
/Lower PCB GND: C1.2, C2.2, C3.2, C4.2, U1.6 (PGND1), U1.15 (PGND2), U1.20 (LGND); also elsewhere on the board
/Lower PCB/Motors/Motor 1A: U1.7 (OUT1A); also elsewhere on the board
/Lower PCB/Motors/Motor 1B: U1.14 (OUT1B); also elsewhere on the board
/Lower PCB/Motors/Motor 2A: U1.5 (OUT2A); also elsewhere on the board
/Lower PCB/Motors/Motor 2B: U1.16 (OUT2B); also elsewhere on the board
unnamed: C4.1, U1.9 (CRES)
unnamed: C5.1, U1.12 (C1L)
unnamed: C5.2, U1.11 (C1H)
unnamed: C6.1, U1.13 (C2L)
unnamed: C6.2, U1.10 (C2H)

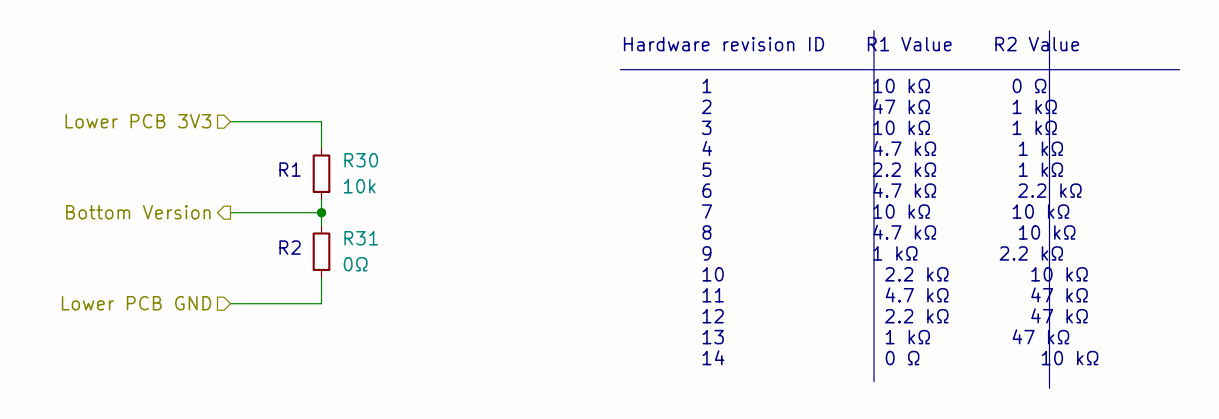
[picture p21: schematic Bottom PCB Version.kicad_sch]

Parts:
R30: 10k; R_0805_2012Metric_Pad1.20x1.40mm_HandSolder
R31: 0Ω; R_0805_2012Metric_Pad1.20x1.40mm_HandSolder

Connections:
/Bottom PCB Version: R30.1, R31.2; also elsewhere on the board
/Lower PCB 3V3: R30.2; also elsewhere on the board
/Lower PCB GND: R31.1; also elsewhere on the board

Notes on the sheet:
Hardware revision ID R1 Value R2 Value 1 10 kΩ 0 Ω 2 47 kΩ 1 kΩ 3 10 kΩ 1 kΩ 4 4.7 kΩ 1 kΩ 5 2.2 kΩ 1 kΩ 6 4.7 kΩ 2.2 kΩ 7 10 kΩ 10 kΩ 8 4.7 kΩ 10 kΩ 9 1 kΩ 2.2 kΩ 10 2.2 kΩ 10 kΩ 11 4.7 kΩ 47 kΩ 12 2.2 kΩ 47 kΩ 13 1 kΩ 47 kΩ 14 0 Ω 10 kΩ

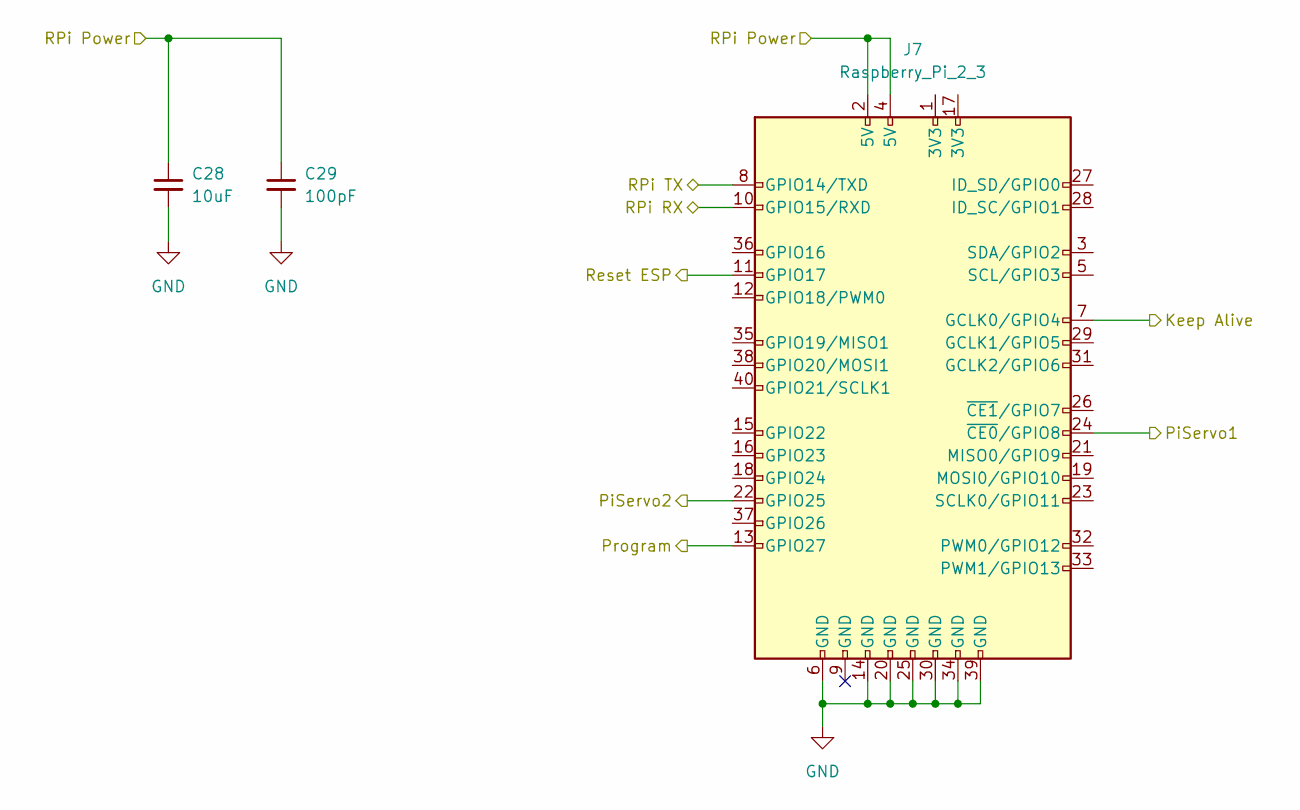
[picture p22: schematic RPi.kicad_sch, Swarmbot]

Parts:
C28: 10uF; C_0805_2012Metric_Pad1.18x1.45mm_HandSolder
C29: 100pF; C_0805_2012Metric_Pad1.18x1.45mm_HandSolder
J7: Raspberry_Pi_2_3; PinHeader_2x20_P2.54mm_Vertical

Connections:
/Top PCB/ESP32/5V Switch Aux: J7.7 (GCLK0/GPIO4); also elsewhere on the board
/Top PCB/ESP32/5V Switched 1: C28.1, C29.1, J7.2 (5V), J7.4 (5V); also elsewhere on the board
/Top PCB/ESP32/Flash: J7.13 (GPIO27); also elsewhere on the board
/Top PCB/ESP32/RX: J7.8 (GPIO14/TXD); also elsewhere on the board
/Top PCB/ESP32/Reset: J7.11 (GPIO17); also elsewhere on the board
/Top PCB/ESP32/TX: J7.10 (GPIO15/RXD); also elsewhere on the board
/Top PCB/RPi/PiServo1: J7.24 (~CE0/GPIO8); also elsewhere on the board
/Top PCB/RPi/PiServo2: J7.22 (GPIO25); also elsewhere on the board
GND: C28.2, C29.2, J7.6 (GND), J7.14 (GND), J7.20 (GND), J7.25 (GND), J7.30 (GND), J7.34 (GND), J7.39 (GND); also elsewhere on the board

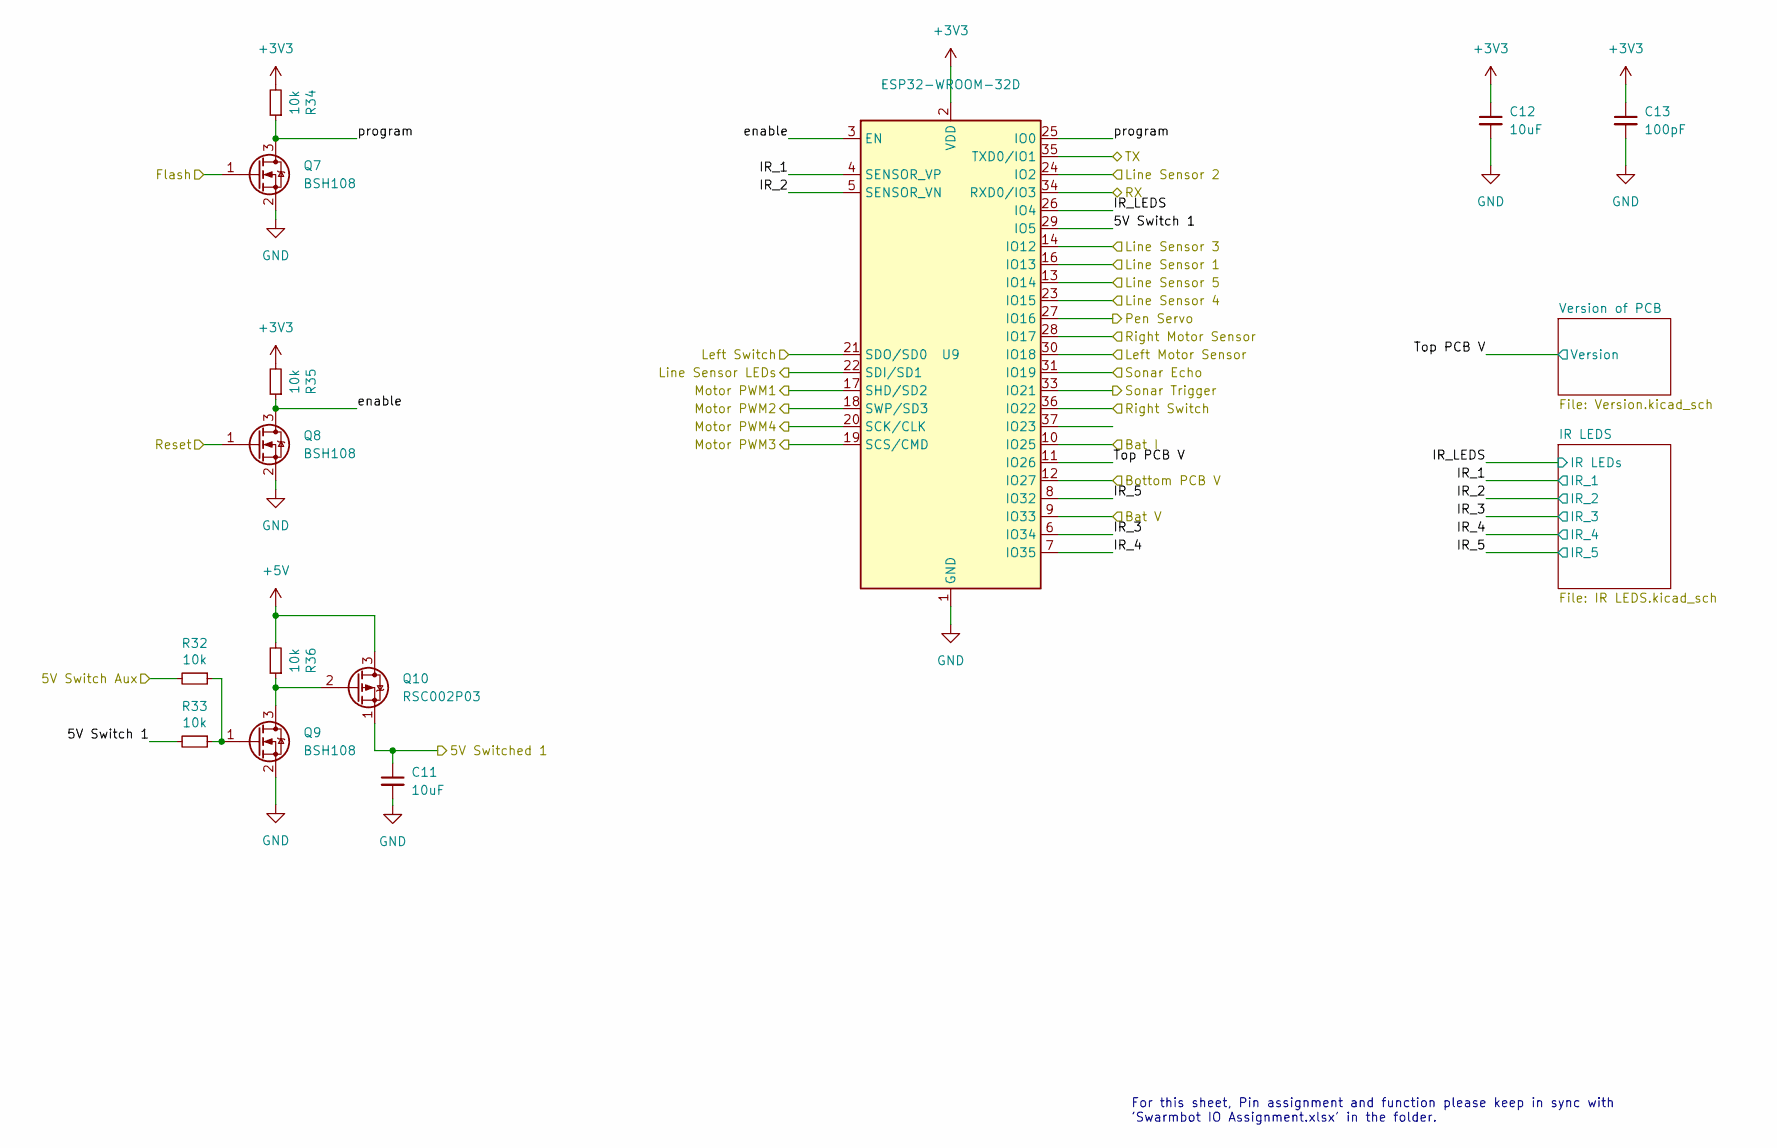
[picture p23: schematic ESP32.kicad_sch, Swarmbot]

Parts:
C11, C12: 10uF; C_0805_2012Metric_Pad1.18x1.45mm_HandSolder
C13: 100pF; C_0805_2012Metric_Pad1.18x1.45mm_HandSolder
Q7, Q8, Q9: BSH108; SOT-23; Farnell 1758067
Q10: RSC002P03; SOT-23; Farnell 2706652
R32, R33, R34, R35, R36: 10k; R_0805_2012Metric_Pad1.20x1.40mm_HandSolder
U9: ESP32-WROOM-32D; ESP32-WROOM-32

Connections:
+3V3: C12.1, C13.1, R34.2, R35.2, U9.2 (VDD); also elsewhere on the board
+5V: Q10.3 (D), R36.2; also elsewhere on the board
/Bottom PCB V: U9.12 (IO27); also elsewhere on the board
/H-Bridge 1A Top: U9.17 (SHD/SD2); also elsewhere on the board
/H-Bridge 1B Top: U9.18 (SWP/SD3); also elsewhere on the board
/H-Bridge 2A Top: U9.19 (SCS/CMD); also elsewhere on the board
/H-Bridge 2B Top: U9.20 (SCK/CLK); also elsewhere on the board
/Left Motor Sensor Top: U9.28 (IO17); also elsewhere on the board
/Left Switch Top: U9.21 (SDO/SD0); also elsewhere on the board
/Line Sensor 1 Top: U9.16 (IO13); also elsewhere on the board
/Line Sensor 2 Top: U9.24 (IO2); also elsewhere on the board
/Line Sensor 3 Top: U9.14 (IO12); also elsewhere on the board
/Line Sensor 4 Top: U9.23 (IO15); also elsewhere on the board
/Line Sensor 5 Top: U9.13 (IO14); also elsewhere on the board
/Line Sensor LEDs Top: U9.22 (SDI/SD1); also elsewhere on the board
/Right Motor Sensor Top: U9.30 (IO18); also elsewhere on the board
/Right Switch Top: U9.36 (IO22); also elsewhere on the board
/Sonar Echo Top: U9.31 (IO19); also elsewhere on the board
/Sonar Trigger Top: U9.33 (IO21); also elsewhere on the board
/Top PCB/ESP32/5V Switch 1: R33.2, U9.29 (IO5)
/Top PCB/ESP32/5V Switch Aux: R32.2; also elsewhere on the board
/Top PCB/ESP32/5V Switched 1: C11.1, Q10.1 (S); also elsewhere on the board
/Top PCB/ESP32/Bat I: U9.10 (IO25); also elsewhere on the board
/Top PCB/ESP32/Bat V: U9.9 (IO33); also elsewhere on the board
/Top PCB/ESP32/Flash: Q7.1 (G); also elsewhere on the board
/Top PCB/ESP32/IR_1: U9.4 (SENSOR_VP); also elsewhere on the board
/Top PCB/ESP32/IR_2: U9.5 (SENSOR_VN); also elsewhere on the board
/Top PCB/ESP32/IR_3: U9.6 (IO34); also elsewhere on the board
/Top PCB/ESP32/IR_4: U9.7 (IO35); also elsewhere on the board
/Top PCB/ESP32/IR_5: U9.8 (IO32); also elsewhere on the board
/Top PCB/ESP32/IR_LEDS: U9.26 (IO4); also elsewhere on the board
/Top PCB/ESP32/RX: U9.34 (RXD0/IO3); also elsewhere on the board
/Top PCB/ESP32/Reset: Q8.1 (G); also elsewhere on the board
/Top PCB/ESP32/TX: U9.35 (TXD0/IO1); also elsewhere on the board
/Top PCB/ESP32/Top PCB V: U9.11 (IO26); also elsewhere on the board
/Top PCB/ESP32/enable: Q8.3 (D), R35.1, U9.3 (EN)
/Top PCB/ESP32/program: Q7.3 (D), R34.1, U9.25 (IO0)
/Top PCB/Pen Servo: U9.27 (IO16); also elsewhere on the board
GND: C11.2, C12.2, C13.2, Q7.2 (S), Q8.2 (S), Q9.2 (S), U9.1 (GND), U9.15 (GND), U9.38 (GND), U9.39 (GND); also elsewhere on the board
unnamed: Q9.1 (G), R32.1, R33.1
unnamed: Q9.3 (D), Q10.2 (G), R36.1

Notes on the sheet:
For this sheet, Pin assignment and function please keep in sync with 'Swarmbot IO Assignment.xlsx' in the folder.

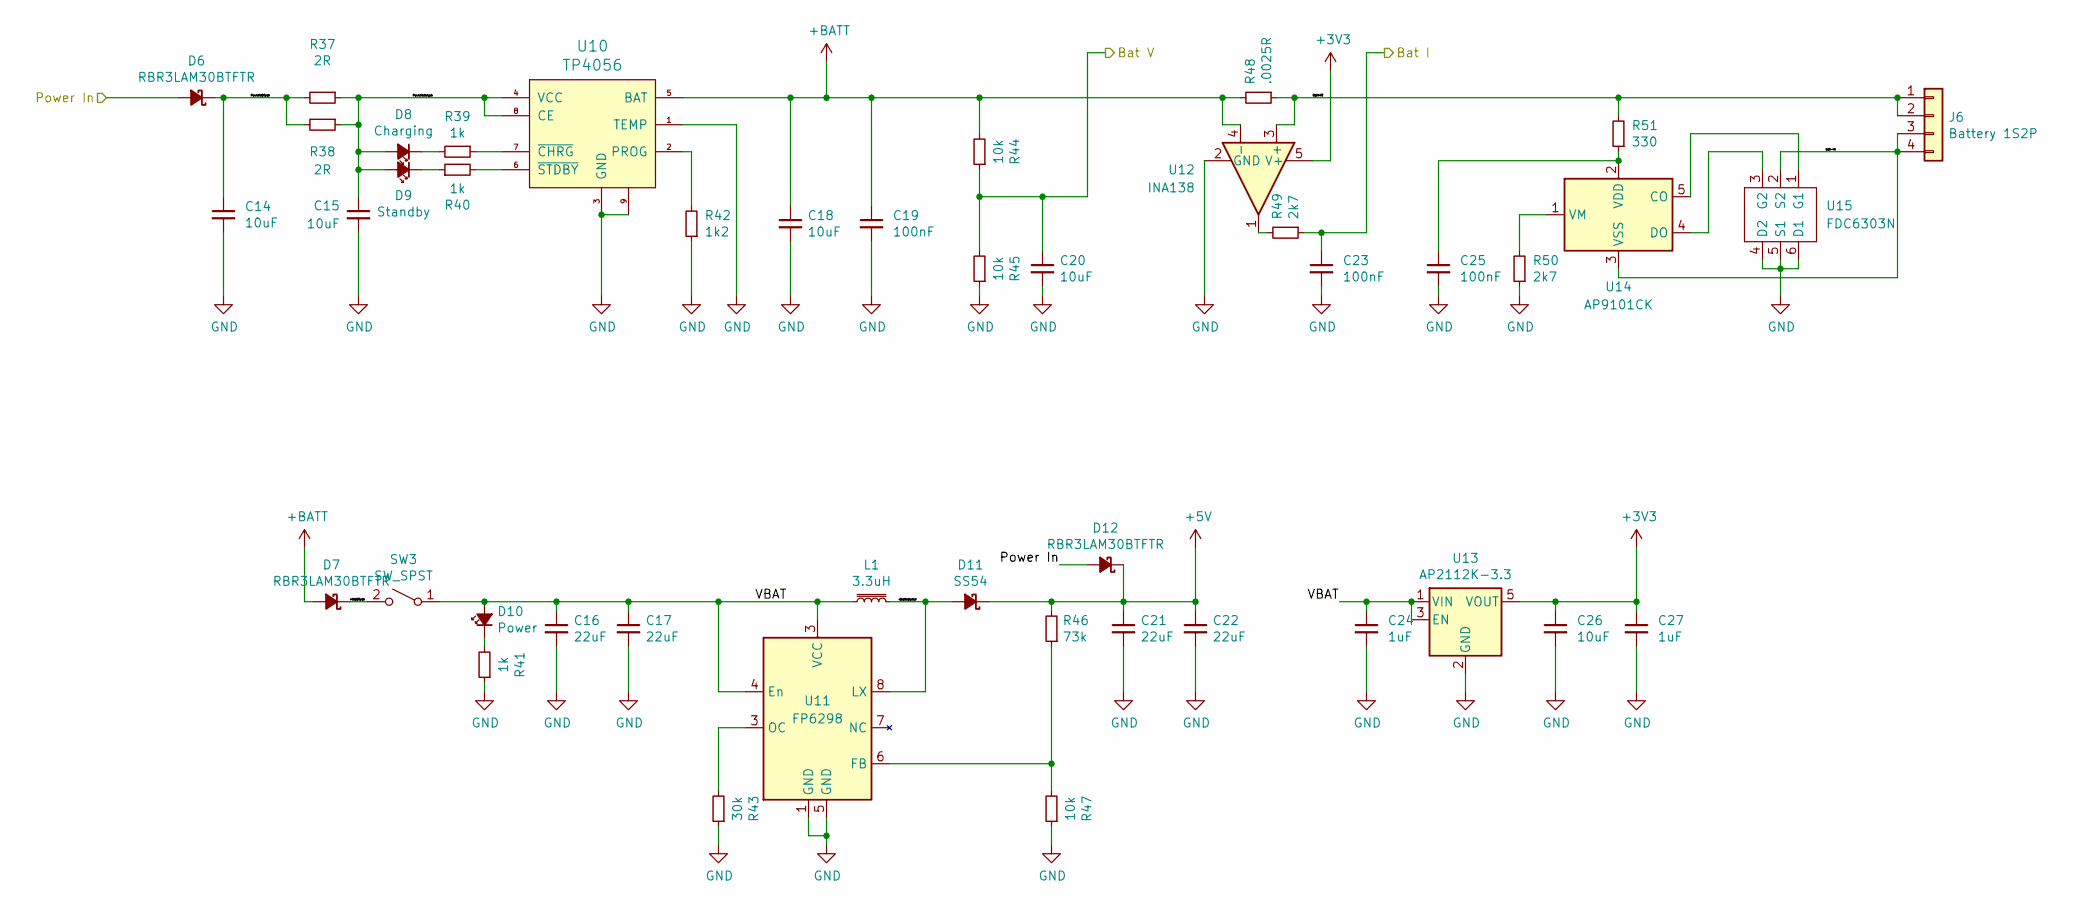
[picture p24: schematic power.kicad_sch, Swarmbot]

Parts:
C14, C15, C18, C20: 10uF; C_0805_2012Metric_Pad1.18x1.45mm_HandSolder
C16, C17, C21, C22: 22uF; C_0805_2012Metric_Pad1.18x1.45mm_HandSolder
C19, C23, C25: 100nF; C_0805_2012Metric_Pad1.18x1.45mm_HandSolder
C24, C27: 1uF; C_0805_2012Metric_Pad1.18x1.45mm_HandSolder; mpn MF-CAP-0603-1uF
C26: 10uF; C_0805_2012Metric_Pad1.18x1.45mm_HandSolder; mpn MF-CAP-1206-10uF
D6, D7, D12: RBR3LAM30BTFTR; D_SOD-128; Farnell 2772718
D8: Charging; LED_0805_2012Metric_Pad1.15x1.40mm_HandSolder
D9: Standby; LED_0805_2012Metric_Pad1.15x1.40mm_HandSolder
D10: Power; LED_0805_2012Metric_Pad1.15x1.40mm_HandSolder
D11: SS54; D_SMC_Handsoldering
J6: Battery 1S2P; JST_XH_B4B-XH-A_1x04_P2.50mm_Vertical
L1: 3.3uH; L_6.3x6.3_H3; Farnell 2530098
R37, R38: 2R; R_0805_2012Metric_Pad1.20x1.40mm_HandSolder
R39, R40, R41: 1k; R_0805_2012Metric_Pad1.20x1.40mm_HandSolder
R42: 1k2; R_0805_2012Metric_Pad1.20x1.40mm_HandSolder
R43: 30k; R_0805_2012Metric_Pad1.20x1.40mm_HandSolder
R44, R45, R47: 10k; R_0805_2012Metric_Pad1.20x1.40mm_HandSolder
R46: 73k; R_0805_2012Metric_Pad1.20x1.40mm_HandSolder
R48: .0025R; R_1206_3216Metric_Pad1.30x1.75mm_HandSolder
R49, R50: 2k7; R_0805_2012Metric_Pad1.20x1.40mm_HandSolder
R51: 330; R_0805_2012Metric_Pad1.20x1.40mm_HandSolder
SW3: SW_SPST; SW_SPST_B3U-3000P-B
U10: TP4056; SOP-8-1EP_4.57x4.57mm_P1.27mm_EP4.57x4.45mm_ThermalVias
U11: FP6298; LCSC# C88319
U12: INA138; SOT-23-5
U13: AP2112K-3.3; SOT-23-5; mpn AP2112K-3.3TRG1
U14: AP9101CK; SOT-23-5; Farnell 3483011
U15: FDC6303N; SOT-23-6_Handsoldering

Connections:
+3V3: C26.1, C27.1, U12.5 (V+), U13.5 (VOUT); also elsewhere on the board
+5V: C21.1, C22.1, D11.1 (K), D12.1 (K), R46.2; also elsewhere on the board
+BATT: C18.1, C19.1, D7.2 (A), R44.2, R48.2, U10.5 (BAT), U12.4 (-)
/Top PCB/ESP32/Bat I: C23.1, R49.1; also elsewhere on the board
/Top PCB/ESP32/Bat V: C20.1, R44.1, R45.2; also elsewhere on the board
/Top PCB/Power/+BatDiode: D7.1 (K), SW3.2 (B)
/Top PCB/Power/Bat+VE: J6.1, J6.2, R48.1, R51.2, U12.3 (+)
/Top PCB/Power/Power In: D6.2 (A), D12.2 (A); also elsewhere on the board
/Top PCB/Power/PowerInDiode: C14.1, D6.1 (K), R37.2, R38.2
/Top PCB/Power/PowerInInrush: C15.1, D8.2 (A), D9.2 (A), R37.1, R38.1, U10.4 (VCC), U10.8 (CE)
/Top PCB/Power/VBAT: C16.1, C17.1, C24.1, D10.2 (A), L1.1, SW3.1 (A), U11.3 (OC), U11.4 (En), U13.1 (VIN), U13.3 (EN)
/Top PCB/Power/bat-ve: J6.3, J6.4, U14.3 (VSS), U15.2 (S2)
/Top PCB/Power/vbatInductor: D11.2 (A), L1.2, U11.8 (LX)
GND: C14.2, C15.2, C16.2, C17.2, C18.2, C19.2, C20.2, C21.2, C22.2, C23.2, C24.2, C25.2, C26.2, C27.2, R41.1, R42.1, R43.1, R45.1, R47.1, R50.1, U10.1 (TEMP), U10.3 (GND), U10.9, U11.1 (GND), U11.5 (GND), U12.2 (GND), U13.2 (GND), U15.4 (D2), U15.5 (S1), U15.6 (D1); also elsewhere on the board
unnamed: C25.1, R51.1, U14.2 (VDD)
unnamed: D8.1 (K), R39.2
unnamed: D9.1 (K), R40.1
unnamed: D10.1 (K), R41.2
unnamed: R39.1, U10.7 (~CHRG)
unnamed: R40.2, U10.6 (~STDBY)
unnamed: R42.2, U10.2 (PROG)
unnamed: R43.2, U11.3 (OC)
unnamed: R46.1, R47.2, U11.6 (FB)
unnamed: R49.2, U12.1
unnamed: R50.2, U14.1 (VM)
unnamed: U14.4 (DO), U15.3 (G2)
unnamed: U14.5 (CO), U15.1 (G1)

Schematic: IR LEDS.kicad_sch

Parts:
D1, D2, D3, D4, D5: IR; LED_D5.0mm
Q1: AO3400A; SOT-23
Q2, Q3, Q4, Q5, Q6: Q_Photo_NPN_CE; LED_D3.0mm_IRBlack
R19, R20, R21, R22, R23: 470; R_0805_2012Metric_Pad1.20x1.40mm_HandSolder
R24, R25, R26, R27, R28, R29: 10k; R_0805_2012Metric_Pad1.20x1.40mm_HandSolder

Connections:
+3V3: Q2.1 (C), Q3.1 (C), Q4.1 (C), Q5.1 (C), Q6.1 (C), R19.1, R20.1, R21.1, R22.1, R23.1; also elsewhere on the board
/Top PCB/ESP32/IR_1: Q2.2 (E), R25.2; also elsewhere on the board
/Top PCB/ESP32/IR_2: Q3.2 (E), R26.2; also elsewhere on the board
/Top PCB/ESP32/IR_3: Q4.2 (E), R27.2; also elsewhere on the board
/Top PCB/ESP32/IR_4: Q5.2 (E), R28.2; also elsewhere on the board
/Top PCB/ESP32/IR_5: Q6.2 (E), R29.2; also elsewhere on the board
/Top PCB/ESP32/IR_LEDS: R24.1; also elsewhere on the board
GND: Q1.2 (S), R25.1, R26.1, R27.1, R28.1, R29.1; also elsewhere on the board
unnamed: D1.1 (K), D2.1 (K), D3.1 (K), D4.1 (K), D5.1 (K), Q1.3 (D)
unnamed: D1.2 (A), R19.2
unnamed: D2.2 (A), R20.2
unnamed: D3.2 (A), R21.2
unnamed: D4.2 (A), R22.2
unnamed: D5.2 (A), R23.2
unnamed: Q1.1 (G), R24.2

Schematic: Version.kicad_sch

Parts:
R17: 10k; R_0805_2012Metric_Pad1.20x1.40mm_HandSolder
R18: 0Ω; R_0805_2012Metric_Pad1.20x1.40mm_HandSolder

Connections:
+3V3: R17.2; also elsewhere on the board
/Top PCB/ESP32/Top PCB V: R17.1, R18.2; also elsewhere on the board
GND: R18.1; also elsewhere on the board

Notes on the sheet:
Hardware revision ID R1 Value R2 Value 1 10 kΩ 0 Ω 2 47 kΩ 1 kΩ 3 10 kΩ 1 kΩ 4 4.7 kΩ 1 kΩ 5 2.2 kΩ 1 kΩ 6 4.7 kΩ 2.2 kΩ 7 10 kΩ 10 kΩ 8 4.7 kΩ 10 kΩ 9 1 kΩ 2.2 kΩ 10 2.2 kΩ 10 kΩ 11 4.7 kΩ 47 kΩ 12 2.2 kΩ 47 kΩ 13 1 kΩ 47 kΩ 14 0 Ω 10 kΩ

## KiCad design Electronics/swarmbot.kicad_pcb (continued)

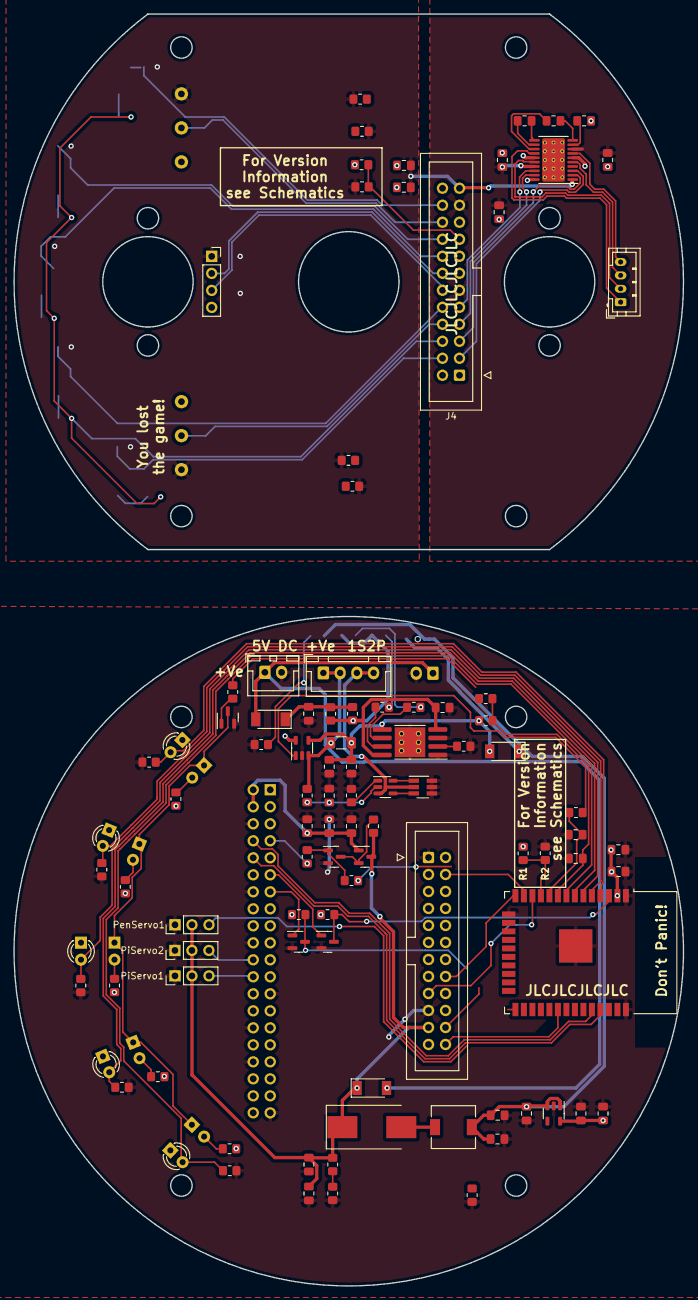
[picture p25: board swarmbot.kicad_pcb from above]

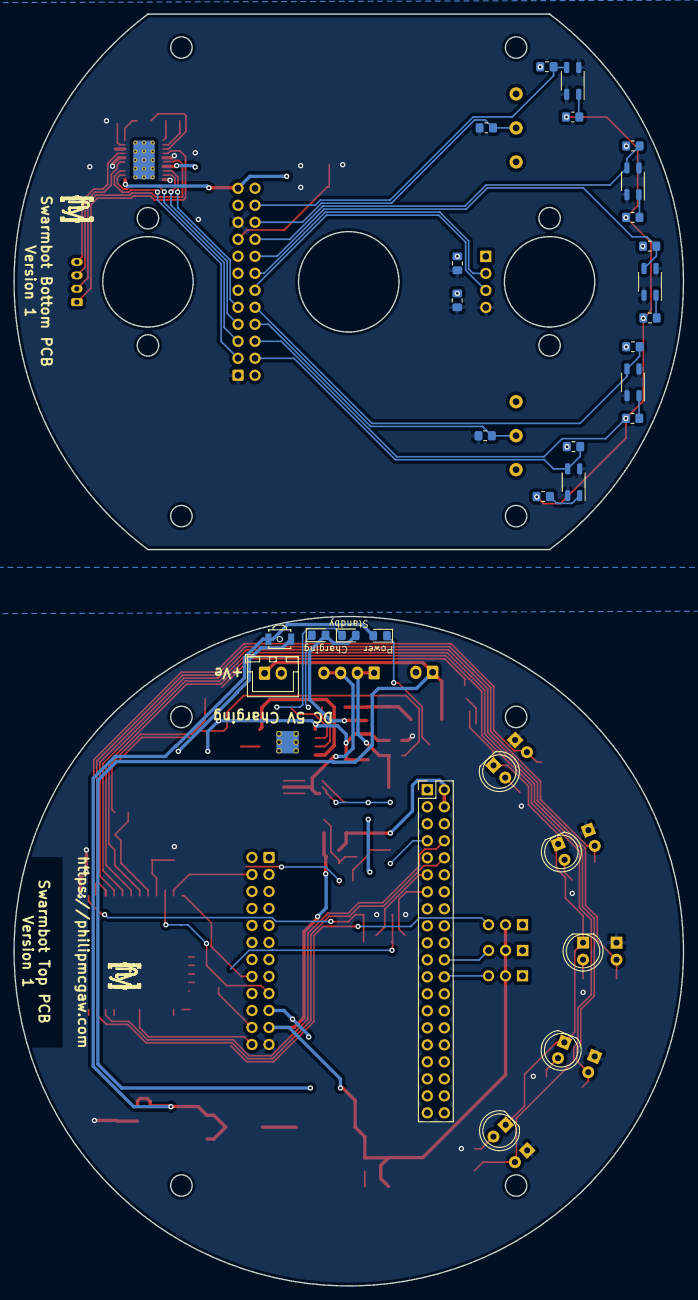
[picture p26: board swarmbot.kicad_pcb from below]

Board: 2 copper layers, 100.0 x 190.0 mm, 131 parts (32 on the bottom side), 105 nets.

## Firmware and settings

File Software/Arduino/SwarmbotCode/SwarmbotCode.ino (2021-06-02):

/*******************************************************************************

  Main Swarmbot code

  Created 2021-06-01
  By Philip McGaw (mostly)

                                               .-----.
                  .----[PWR]-------------------| USB |--.
                  |                            '-----'  |
                  |         GND/RST2  [ ][ ]            |
                  |       MOSI2/SCK2  [ ][ ]  A5/SCL[ ] |   C5 n/c duplicated
                  |          5V/MISO2 [ ][ ]  A4/SDA[ ] |   C4 n/c duplicated
                  |                             AREF[ ] |
                  |                             AREF[ ] |
                  |                              GND[ ] |
                  | [ ]NC                     SCK/13[ ] |   B5 -> Pi Power on
                  | [ ]v.ref                 MISO/12[ ] |   .  <- On Charge
                  | [ ]RST                   MOSI/11[ ]~|   .  -> stepperLHS 4
                  | [ ]3V3    +---+               10[ ]~|   .  -> stepperLHS 2
                  | [ ]5v     | A |                9[ ]~|   .  -> stepperLHS 3
                  | [ ]GND   -| R |-               8[ ] |   B0 -> stepperLHS 1
                  | [ ]GND   -| D |-                    |
                  | [ ]Vin   -| U |-               7[ ] |   D7 -> stepperRHS 4
                  |          -| I |-               6[ ]~|   .  -> stepperRHS 2
        IR 1 ->   | [ ]A0    -| N |-               5[ ]~|   .  -> stepperRHS 3
        IR 2 ->   | [ ]A1    -| O |-               4[ ] |   .  -> stepperRHS 1
        IR 3 ->   | [ ]A2     +---+           INT1/3[ ]~|   .  -> Sonar Trigger
        IR 4 ->   | [ ]A3                     INT0/2[ ] |   .  <- Sonar Echo
     IR LEDS <-   | [ ]A4/SDA  RST SCK MISO     TX>1[ ] |   .  n/c TX (Via USB)
 Bat Voltage ->   | [ ]A5/SCL  [ ] [ ] [ ]      RX<0[ ] |   D0 n/c RX (Via USB)
                  |            [ ] [ ] [ ]              |
                  '--.                         .--------'
                      \_______________________/

                  HTTP://BUSYDUCKS.COM/ASCII-ART-ARDUINOS
*******************************************************************************/
// Include the AccelStepper Library
#include "src/AccelStepper/AccelStepper.h"

// Include the HC-SR04 code (non blocking https://www.instructables.com/Non-blocking-Ultrasonic-Sensor-for-Arduino/)
#include "src/HC_SR04/HC_SR04.h"

// Define the pins for the HC-SR04 sonar module
#define TRIG_PIN 3
#define ECHO_PIN 2
#define ECHO_INT 0

// Define the input pins and their usesage
#define BAT_PIN A5
#define IR1 A3
#define IR2 A2
#define IR3 A1
#define IR4 A0

// Define the output Pins
#define ON_CHARGE 12
#define PI_ON 13
#define IRLEDS A4

// Debug (this can now be changed from the serial console)
bool debug = 1;


// String is not a primative (will look that up later?) NotQuiteHere tells me it
// needs a capital letter… and I am not allowed to #define string String to make
// the compiler fix it for me.
String sendData{};
int bufferLen{};

// Define step constant
// If you want to drive the motor at full step, this should be 4
// If you want to drive the motor at half steps, this should be 8.
#define FULLSTEP 8
const int STEPPER_SPEED = 900;
// const int ACCELERATION = 10;

// vairiables

int batVoltage  = 0;
bool ir_leds    = 0;
int ir1Val      = 0;
int ir2Val      = 0;
int ir3Val      = 0;
int ir4Val      = 0;
char direction  = 's';

// this code came from https://www.instructables.com/id/BananaRaspberry-Pi-Arduino-Rover-With-Webcam/
// and then NotQuiteHere happened to it
char incomingByte; // variable to receive data from the serial port

// This is distance that the sonar can see in cm.
// this is a volatile as it changes very offten, and if its not, the value does
// not update as quickly as it should.
// https://www.arduino.cc/reference/en/language/variables/variable-scope-qualifiers/volatile/
volatile int sonarDistance = 0;

// Define Wheels constant

// What is the Diamiter of the wheel?
const float wheelDia = 40;

const float pi = 3.14;
const float wheel_circ = wheelDia * pi;

// The 28BYJ-48 motor has 32 steps per revolution, however with the 1/63.6…
// gearbox, means that for a single revolution of the output shaft, we are
// looking at 2038 steps.

const float stepsPermm = 2038 / wheel_circ;

// Creates two instances of the stepermotor
// Pins entered in sequence IN1-IN3-IN2-IN4 for proper step sequence, pinout
// diagram can be found in the Arduino code folder.
// code from https://lastminuteengineers.com/28byj48-stepper-motor-arduino-tutorial/

AccelStepper stepperLHS(FULLSTEP, 8, 10, 9, 11);
AccelStepper stepperRHS(FULLSTEP, 4, 6, 5, 7);

// Create the instance of the Sonar sensor.

HC_SR04 sonar(TRIG_PIN, ECHO_PIN, ECHO_INT);

void setup() {
  // put your setup code here, to run once:

  // Lets start serial port
  Serial.begin(9600);
  while(!Serial);

  // Setup the sonar module
  sonar.begin();

  // set the maximum speed, acceleration factor,
  // initial speed and the target position
  stepperLHS.setMaxSpeed(STEPPER_SPEED);
  stepperRHS.setMaxSpeed(STEPPER_SPEED);


  pinMode(ON_CHARGE, INPUT);
  pinMode(PI_ON, OUTPUT);
}

void loop()
{
  // do things baised on serial messages…
  if ( Serial.available() > 0 ) // if data is available to read
  {
    incomingByte = Serial.read(); // read it and store it in 'incomingByte'
  }

  // I wonder if there is a better way to do this…
  // how computationaly expensive is a divide by two?

  switch (incomingByte) {
    case 'q':
      // drive left
      stepperLHS.setSpeed(STEPPER_SPEED / 2);
      stepperRHS.setSpeed(STEPPER_SPEED);
      direction  = 'q';
      break;
    case 'w':
      // forwards
      stepperLHS.setSpeed(STEPPER_SPEED);
      stepperRHS.setSpeed(STEPPER_SPEED);
      direction  = 'w';
      break;
    case 'e':
      // drive right
      stepperLHS.setSpeed(STEPPER_SPEED);
      stepperRHS.setSpeed(STEPPER_SPEED / 2);
      direction  = 'e';
      break;
    case 'a':
      // turn left
      stepperLHS.setSpeed(0);
      stepperRHS.setSpeed(STEPPER_SPEED);
      direction  = 'a';
      break;
    case 's':
      // stop
      stepperLHS.setSpeed(0);
      stepperRHS.setSpeed(0);
      direction  = 's';
      break;
    case 'd':
      // turn right
      stepperLHS.setSpeed(STEPPER_SPEED);
      stepperRHS.setSpeed(0);
      direction  = 'd';
      break;
    case 'z':
      // hard left
      stepperLHS.setSpeed(-STEPPER_SPEED);
      stepperRHS.setSpeed(STEPPER_SPEED);
      direction  = 'a';
      break;
    case 'x':
      // back
      stepperLHS.setSpeed(-STEPPER_SPEED);
      stepperRHS.setSpeed(-STEPPER_SPEED);
      direction  = 'x';
      break;
    case 'c':
      // hard right
      stepperLHS.setSpeed(STEPPER_SPEED);
      stepperRHS.setSpeed(-STEPPER_SPEED);
      direction  = 'c';
      break;

    case 'm':
      // this turns debug on and off from the serial monitor
      debug = !debug;
      incomingByte = '_';
      break;
  }

  // This bit does the sonar rangefinder stuffs
  if (sonar.isFinished())
  {
    // put the current reading into a vairiable and run the sensor again…
    sonarDistance = sonar.getRange();
    sonar.start();
  }

  if (sendData.length() > 0) {
    bufferLen = Serial.availableForWrite();
    if (sendData.length() > bufferLen) {
      Serial.print(sendData.substring(0,bufferLen));
      sendData = sendData.substring(bufferLen);
    } else {
      Serial.println(sendData);
      sendData = "";
    }
  } else {
    sendData = serialOutput(debug);
  }

  // Sets the speed of the stepperRHS
  stepperLHS.runSpeed();
  stepperRHS.runSpeed();
}

String serialOutput(bool debug) {
  String sendData{};

  // Read the analog pins and map them to 0-100 as more readable (loss of
  // resolution should not be an issue).
  // we only do this every so offten, this is to try and reduce the amount of
  // serial and processing time used (map should be fairly low utilisation?)


  batVoltage = analogRead(BAT_PIN);

  ir1Val = analogRead(IR1);
  ir2Val = analogRead(IR2);
  ir3Val = analogRead(IR3);
  ir4Val = analogRead(IR4);

  batVoltage = map(batVoltage, 0, 1023, 0, 100);

  ir1Val = map(ir1Val, 0, 1023, 0, 100);
  ir2Val = map(ir2Val, 0, 1023, 0, 100);
  ir3Val = map(ir3Val, 0, 1023, 0, 100);
  ir4Val = map(ir4Val, 0, 1023, 0, 100);

  if (debug)
  {
    // Assemble data into a human readable(ish) format and add to the string
    sendData = "uptime: " + String(millis());
    sendData += " ms\tBat V: " + String(batVoltage);
    sendData += " %\tIRLEDs " + String(ir_leds);
    sendData += "\t1: " + String(ir1Val);
    sendData += "\t2: " + String(ir2Val);
    sendData += "\t3: " + String(ir3Val);
    sendData += "\t4: " + String(ir4Val);
    sendData += "\tSonar: " + String(sonarDistance);
    sendData += " cm\tDirection: " + String(direction);
    // sendData += " cm\tLHS Distance: " + String(stepperLHS.distanceToGo());
    // sendData += " steps\tCurrent pos: " + String(stepperLHS.currentPosition());
    // sendData += " steps\tRHS Distance: " + String(stepperRHS.distanceToGo());
    // sendData += " steps\tCurrent pos: " + String(stepperLHS.currentPosition());
    sendData += "\tByte: " + String(incomingByte);
  } else {
    // less human readable than above
  }
  return sendData;
}

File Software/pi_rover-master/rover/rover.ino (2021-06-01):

#include <Servo.h>
#include <AFMotor.h>

int motorSpeedMax = 250;
int motorSpeedMed = 150;
int motorSpeedMin = 100;
int pos_t = 90;
int pos_p = 90;
int doOnce = 0;
Servo pan;
Servo tilt;
AF_DCMotor motor1(1);
AF_DCMotor motor2(2);
AF_DCMotor motor3(3);
AF_DCMotor motor4(4);
char incomingByte; // variable to receive data from the serial port

void setup()
{
  Serial.begin(9600);           // set up Serial library at 9600 bps

  // turn on motor
  motor1.setSpeed(motorSpeedMed);
  motor2.setSpeed(motorSpeedMed);
  motor3.setSpeed(motorSpeedMed);
  motor4.setSpeed(motorSpeedMed);
  pan.attach(9);
  tilt.attach(10);
  pan.write(pos_p);
  tilt.write(pos_t);

}

void loop()
{

  if ( Serial.available() > 0 ) // if data is available to read
  {
    incomingByte = Serial.read(); // read it and store it in 'incomingByte'
    doOnce = 0;
  }

  if ( incomingByte == 'i' )
  {
    motor1.setSpeed(motorSpeedMax);
    motor2.setSpeed(motorSpeedMax);
    motor3.setSpeed(motorSpeedMax);
    motor4.setSpeed(motorSpeedMax);
  }

  if ( incomingByte == 'o' )
  {
    motor1.setSpeed(motorSpeedMed);
    motor2.setSpeed(motorSpeedMed);
    motor3.setSpeed(motorSpeedMed);
    motor4.setSpeed(motorSpeedMed);
  }

  if ( incomingByte == 'p' )
  {
    motor1.setSpeed(motorSpeedMin);
    motor2.setSpeed(motorSpeedMin);
    motor3.setSpeed(motorSpeedMin);
    motor4.setSpeed(motorSpeedMin);
  }

  if ( incomingByte == '1' )
  {
    motor1.run(FORWARD);
    motor2.run(FORWARD);
    motor3.run(FORWARD);
    motor4.run(FORWARD);
  }

  if ( incomingByte == '2' )
  {
    motor1.run(RELEASE);
    motor2.run(RELEASE);
    motor3.run(FORWARD);
    motor4.run(FORWARD);
  }

  if ( incomingByte == '3' )
  {
    motor1.run(FORWARD);
    motor2.run(FORWARD);
    motor3.run(RELEASE);
    motor4.run(RELEASE);
  }


  if ( incomingByte == '4' )
  {
    motor1.run(BACKWARD);
    motor2.run(BACKWARD);
    motor3.run(BACKWARD);
    motor4.run(BACKWARD);
  }

  if ( incomingByte == 's' )
  {
    motor1.run(RELEASE);
    motor2.run(RELEASE);
    motor3.run(RELEASE);
    motor4.run(RELEASE);
  }

  if ( incomingByte == 'q' && doOnce == 0)
  {
    pos_p = pos_p + 10;
    pan.write(pos_p);
    doOnce = 1;
  }

  if ( incomingByte == 'w' && doOnce == 0)
  {
    pos_p = pos_p - 10;
    pan.write(pos_p);
    doOnce = 1;
  }

  if ( incomingByte == 'a' && doOnce == 0)
  {
    pos_t = pos_t + 10;
    tilt.write(pos_t);
    doOnce = 1;
  }

  if ( incomingByte == 'z' && doOnce == 0)
  {
    tilt.write(pos_t - 10);
    pos_t = pos_t - 10;
    doOnce = 1;
  }
}

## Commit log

2020-05-02 Oops
    I seem to have added some mac only files…
2020-05-02 All good fun
    [SwarmBot PBS.xlsx]
2020-05-02 Fixed the file format
    [Swarmbot Assembly.f3d]
2020-05-05 small update
    [Bottom PCB.kicad_pcb, Bottom PCB.sch]
2020-05-07 Delete SwarmBot PBS.xlsx
    meh
    [SwarmBot PBS.xlsx]
2020-05-07 Update Bottom PCB.kicad_pcb
    [Bottom PCB.kicad_pcb]
2020-05-07 Changed IR sensors to allow for passive measurments
    [Bottom PCB.kicad_pcb, Bottom PCB.sch]
2020-05-07 Adding 9 DoF IMU
    [Bottom PCB.kicad_pcb, Bottom PCB.sch]
2020-05-08 Change MCU
    swap arduino to ESP32-Wroom
    https://www.mouser.co.uk/ProductDetail/Espressif/ESP32-WROVER/?qs=chTDxNqvsynCfB3ibKeA%252bA%3D%3D
    Mouser No: 356-ESP32-WROVER
    [Bottom PCB.kicad_pcb, Bottom PCB.sch]
2020-05-11 Add reset / reboot circuit for ESP32, modify readme to remove eagle constraint as eagle is no longer in use.
    [Bottom PCB.sch]
2020-05-11 Moved components to sub sheets
    Continued on from Bob's work, in so much that I moved some items to additional sheets, increesed the size of the main header to include a half battery tap, and the addition of jumpers so that the dev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
    [Bat Managment.sch, Bottom PCB.kicad_pcb, Bottom PCB.sch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]
2020-05-11 Set up MCP23017
    Added the main parts of an MCP23017
    [Bottom PCB.sch, ESP32-WROVER.sch]
2020-05-11 simplified the pcb,
    Removed the shift registers and moved functionality onto the 16 way IO expander, also removed the H-Bridge, may re-add a I2C duel h-bridge at a later date.
    Thinking about best way to drive the four servo headers, may use I2C controller for them as well, as then the timing maths is removed from the main micro
    [Bottom PCB.kicad_pcb, Bottom PCB.sch, ESP32-WROVER.sch]
2020-05-11 moved some parts to 5V supply
    [Bottom PCB.kicad_pcb, Bottom PCB.sch]
2020-05-11 removed the servos at the moment
    [Bat Managment.sch, Bottom PCB.kicad_pcb, Bottom PCB.sch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]
2020-05-13 Added power switch
    Some more modifications
    [Bat Managment.sch, Bottom PCB.kicad_pcb, Bottom PCB.sch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]
2020-05-16 added more stuff
    [Bat Managment.sch, Bottom PCB.kicad_pcb, Bottom PCB.sch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]
2020-05-17 changed from 1206 to 0805
    [Bat Managment.sch, Bottom PCB.kicad_pcb, Bottom PCB.sch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]
2021-06-01 Made some exciting changes
    [Wiring.fzz]
2021-06-03 Added Raspberry Pi Zero to the breadboard, and did some work on cleaning up the wires,
    this is not finished, and will need a little more work…
    [Wiring.fzz]
2021-06-03 added serial
    [Wiring.fzz]
2021-06-03 COTS idea…
2021-06-04 See it was being odd
    [COTS Prototype.kicad_pcb, COTS Prototype.sch, MicroControler and RPi Zero.sch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]
2021-06-07 working on schematics
    [Bottom PCB.dxf, COTS Prototype.kicad_pcb, COTS Prototype.sch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]
2021-06-18 changed COTs PCB
    [Bottom PCB.dxf, COTS PCB.dxf, COTS Prototype.kicad_pcb]
2021-10-14 made some changes
    [COTS Prototype.kicad_pcb, COTS Prototype.sch, ESP32.kicad_sch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]
2021-10-20 try to remove the kicad backups
2021-10-20 some little changes have been made
    [ESP32.kicad_sch, Lower PCB.kicad_sch, Motors.kicad_sch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]
2021-10-20 off to do other things for a second
    ;
    [Motors.kicad_sch, swarmbot.kicad_pcb, swarmbot.kicad_sch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]
2021-10-27 updated the excel
    [ESP32.kicad_sch, Swarmbot IO Assignment.xlsx]
2021-10-27 some pcb changes
    [Motors.kicad_sch, swarmbot.kicad_pcb, swarmbot.kicad_sch]
2021-11-01 added bom
    [ESP32.kicad_sch, Lower PCB.kicad_sch, RPi.kicad_sch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]
2021-11-01 del backups
    [ESP32.kicad_sch, Lower PCB.kicad_sch, Motors.kicad_sch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]
2021-11-26 some changes were made
    [Bottom PCB Version.kicad_sch, ESP32.kicad_sch, Hardware Version Calculator.xlsx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]
2021-11-27 removed the backups
    [ESP32.kicad_sch, IR LEDS.kicad_sch, Lower PCB.kicad_sch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]
2021-11-27 slight changes to layout
    [swarmbot.kicad_pcb]
2021-11-28 don't use the enable pingit statusgit status
    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
    [ESP32.kicad_sch, IR LEDS.kicad_sch, Lower PCB.kicad_sch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]
2021-11-29 Fixed the enable pin being used
    [ESP32.kicad_sch, IR LEDS.kicad_sch, Lower PCB.kicad_sch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]
2021-11-30 Cleaning up the stupid error with the pinout
    [ESP32.kicad_sch, IR LEDS.kicad_sch, Lower PCB.kicad_sch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]
2021-12-22 Get Arduino to work

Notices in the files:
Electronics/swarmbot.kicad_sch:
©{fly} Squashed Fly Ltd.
